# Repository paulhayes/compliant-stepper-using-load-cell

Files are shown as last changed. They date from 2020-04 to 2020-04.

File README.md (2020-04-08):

# Compliant Stepper Motor example using a load cell



## Hardware
* Teensy 3.2 or above
* cheap load cell
* cheap unipolar stepper motor with driver board ( 4 with coil inputs )
* 10nF cap across the loadcell outputs.
* button ( optional, allows for manually calibration of the load-cell at rest )
That's it!

## Pins

* A10-A11 loadcell ( yes they are annoying to get to, but at least they aren't on the underside of the board )
* D4-7 stepper motor contol
* D8 button ( connected buttons other terminal to ground )

## Installation and usage

Download or clone this repo, and open in platformio. This can be compiled with the Arduino IDE, however you'll need to install the 3rd party libraries mentioned in the platformio.ini manually.

## Code

This code utlised the teensy's fast ADC differencial comparator across the wheatstone bridge of the loadcell. 

The Teensy is able to read the load cell extremely quickly, depending on settings I was getting between 1khz-100khz. Admitidly only with 16bit precision, but this is more than enough for detecting force being applied to it. I've opted for very high averaging as the values are extremely noisy.

### Filtering

I've tried using both a first order ( low pass ) filter, which worked well. I switched to a Kalman filter, and it has marginally better results, increasing responce times while filtering slightly better.  However the benefits are minor.

## Why didn't you use the teensy's Programable Gain Amplifier?

I was unable to use the programable gain amplifier of the teensy due to the fact it seems to only work in either 0-1.2v or -1.2-0v. Whereas I wanted to read both positive and negative values across the wheatstone bridge. Although the PGA is adaptive it waits until going above a certain value in the negative threshold before inverting the gain.

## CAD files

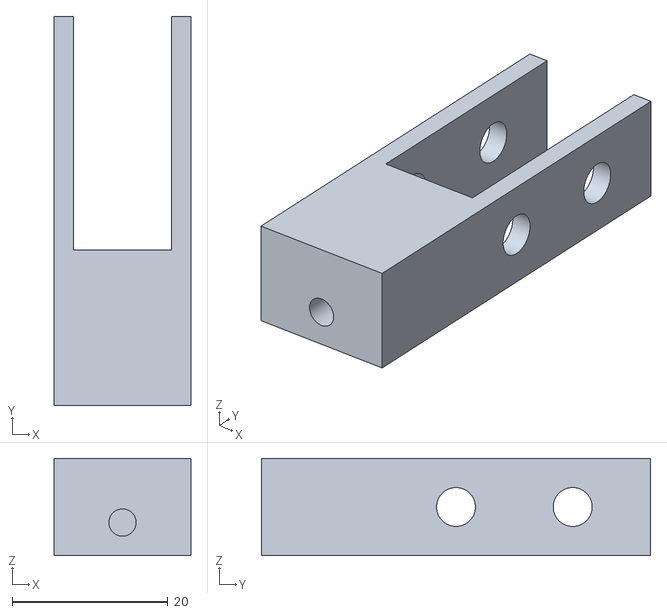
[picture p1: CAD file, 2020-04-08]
model/loadCellMotorCoupler.stl
17.6 x 50.0 x 12.5

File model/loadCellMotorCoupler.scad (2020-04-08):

motorShaftDim = [5,3,6];
motorShaftBase = [5,2];

loadCell = [12.5+0.1,80,12.5];

case = [loadCell.x+5,46,loadCell.z];
caseBackLengthFromHole = 10;
loadCellDistanceFromShaft = 10;
loadCellHoleGap = 15;
loadCellHoleSize = 5;
loadCellHolePos1 = [-case.x/2,5,loadCell.z/2];
loadCellHolePos2 = [-case.x/2,5+loadCellHoleGap,loadCell.z/2];

lockingInsertSize = 3.5;
module motorShaft(){
    intersection(){
    translate([-motorShaftDim.x/2,-motorShaftDim.y/2,motorShaftBase.y]) cube(motorShaftDim);        
    translate([0,0,motorShaftBase.y]) cylinder(d=motorShaftBase.x,h=motorShaftDim.z,$fn=60);
    }
    cylinder(d=motorShaftBase.x,h=motorShaftBase.y,$fn=60);
}

module lockingScrewHole(){
    translate([0,0,motorShaftDim.z-lockingInsertSize/2]) rotate([90,0,0]) cylinder(d=lockingInsertSize,h=caseBackLengthFromHole,$fn=60);
}

module loadCellHoles(){
    translate(loadCellHolePos1) rotate([0,90,0]) cylinder(d=loadCellHoleSize,h=case.x,$fn=60);
    translate(loadCellHolePos2) rotate([0,90,0]) cylinder(d=loadCellHoleSize,h=case.x,$fn=60);
}

difference(){
    translate([-case.x/2,-caseBackLengthFromHole,0]) cube(case);
    motorShaft();
    lockingScrewHole();
    translate([-loadCell.x/2,loadCellDistanceFromShaft,0]) cube(loadCell);
    translate([0,loadCellDistanceFromShaft,0]) loadCellHoles();
}

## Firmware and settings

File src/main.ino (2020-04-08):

//#include <HX711.h>
#define PLOT_MODE true

#include <Arduino.h>
#include <AccelStepper.h>
#include <ADC.h>
#include <ADC_util.h>
#include "Plotter.h"
#include <SimpleKalmanFilter.h>

const int stepperPhaseA = 4;
const int stepperPhaseB = 5;
const int stepperPhaseC = 6;
const int stepperPhaseD = 7;

/*
 SimpleKalmanFilter(e_mea, e_est, q);
 e_mea: Measurement Uncertainty 
 e_est: Estimation Uncertainty 
 q: Process Noise
 */
SimpleKalmanFilter simpleKalmanFilter(2, 2, 0.1);

AccelStepper stepper = AccelStepper(AccelStepper::HALF4WIRE,stepperPhaseA,stepperPhaseC,stepperPhaseB,stepperPhaseD) ;
Plotter p;

ADC *adc = new ADC(); // adc object


double compliantForceThreshold = 5;
double returnThreshold = 4.5;
double center = 0;

int counter = 0;
int rawValue = 0;
double val = 0;
double lowPassFilteredValue = 0;
double sKalmanFilteredValue = 0;

int inputToSteps = 50;
long destinationPosition = 0;
long maxTargetPositionDistance = 100;
const int sendRate = 120;
const int secondsToPlot = 20;
long lastSendMillis;
long lastSendADCCount = 0;
int filter = 200;
long adcReadCount = 0;
float adcReadRate = 0;
long move;

bool newADCValue = false;
bool isCalibrated = false;

void setup(){

#if PLOT_MODE
  p.Begin();
  p.AddTimeGraph( "Some title of a graph", sendRate*10, "raw input",rawValue, "kalman filter", sKalmanFilteredValue, "low pass filter",lowPassFilteredValue, "centered", val, "threshold", compliantForceThreshold, "adc read rate khz", adcReadRate );
#else
  Serial.begin(115200);
#endif
  stepper.setMaxSpeed(1000);
  stepper.setAcceleration(4000);
  
  adc->adc0->setReference(ADC_REFERENCE::REF_1V2);
  // see README.md as to why I don't use this
  //adc->adc0->enablePGA(0);
  adc->adc0->setAveraging(32); // set number of averages
  adc->adc0->setResolution(16); // set bits of resolution
  adc->adc0->setConversionSpeed(ADC_CONVERSION_SPEED::MED_SPEED); // change the conversion speed
  adc->adc0->setSamplingSpeed(ADC_SAMPLING_SPEED::MED_SPEED); // change the sampling speed
  
  adc->adc0->enableInterrupts(adc1_isr);
  adc->adc0->startContinuousDifferential(A10,A11);
  
  pinMode(8,INPUT_PULLUP);
  attachInterrupt(8,onButtonUp,RISING);
}


void loop(){

  if(newADCValue){
    newADCValue = false;
    readADC();
    #if PLOT_MODE
    plot();
    #else
    serialDebug();
    #endif
  }

  if(!isCalibrated)
    return;

  moveMotor();
}

void readADC(){
      rawValue = -adc->adc0->analogReadContinuous();
    #if not PLOT_MODE
    if(adc->adc0->fail_flag != ADC_ERROR::CLEAR) {
      Serial.print("Error ADC1: "); Serial.println(getStringADCError(adc->adc0->fail_flag));
    }
    #endif
    adcReadCount++;
    lowPassFilteredValue = (rawValue+lowPassFilteredValue*filter) / (filter+1);
    sKalmanFilteredValue = simpleKalmanFilter.updateEstimate(rawValue);
    
    val = distanceFromCenter( sKalmanFilteredValue );
    if(!isCalibrated && (adcReadCount>3000L)){
      calibrate();
    }
}

void moveMotor(){
  if(val>compliantForceThreshold){    
      move = (int)round(val)*inputToSteps;      
      stepper.setSpeed( move );
      stepper.runSpeed();
    }
    else if(val<-compliantForceThreshold){
      move = (int)round(val)*inputToSteps;    
      stepper.setSpeed( move );
      stepper.runSpeed();
    } else if(abs(val)<returnThreshold){
      move = 0;
      stepper.moveTo( destinationPosition );
      stepper.run();
    }
}

void calibrate(){
  center = lowPassFilteredValue;
  isCalibrated = true;
}

double distanceFromCenter(double val){
  return val - center;
}

void plot(){
    long currentTime = millis();
    int sendDuration = 1000/sendRate;
    if(sendDuration<=currentTime-lastSendMillis){
      
      adcReadRate = 1.0f*( adcReadCount-lastSendADCCount ) / (currentTime-lastSendMillis);
  
      p.Plot();
      lastSendMillis = currentTime;
      lastSendADCCount = adcReadCount;
    }

}

void serialDebug(){

    if(Serial.available()){
      char command = Serial.read();
      if(command=='z'){
        Serial.println("");
        stepper.setCurrentPosition(0);
        Serial.println("");
        Serial.println("zeroed position ");
      }
      if(command=='-'){
        inputToSteps--;
        Serial.println("");
        Serial.print("set inputToSteps to: ");
        Serial.print(inputToSteps);
        Serial.println("");
      }
      if(command=='+'){
        inputToSteps++;
        Serial.println("");
        Serial.print("set inputToSteps to: ");
        Serial.print(inputToSteps);
        Serial.println("");
      }
      if(command=='<'){
        compliantForceThreshold--;
        Serial.println("");
        Serial.print("threshold to: ");
        Serial.print(compliantForceThreshold);
        Serial.println("");
      }
      if(command=='>'){
        compliantForceThreshold++;
        Serial.println("");
        Serial.print("threshold to: ");
        Serial.print(compliantForceThreshold);
        Serial.println("");
      }
      if(command=='v'){
        compliantForceThreshold++;
        
        Serial.println("");
        Serial.print("current value=");
        Serial.print(val);
        Serial.print(" low pass value=");
        Serial.print(lowPassFilteredValue);
        Serial.println("");
      }
      
    }
}

/* Interrupts */

void onButtonUp(){
  if(isCalibrated){
    calibrate();
  }
}

void adc1_isr(void) {
    adc->adc0->analogReadContinuous();
    newADCValue = true;
}

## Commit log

2020-04-04 :tada: initial commit
    [loadCellMotorCoupler.scad, loadCellMotorCoupler.stl]
2020-04-05 added spring action to code, when force applied to load cell is below threshold, continue to original position
    [loadCellMotorCoupler.scad]
2020-04-07 Improved accuracy, added start up autocalibration, calibration button, and kalman filtering@
2020-04-08 Added locking insert, for attaching to servo shaft properly
    [loadCellMotorCoupler.scad, loadCellMotorCoupler.stl]
